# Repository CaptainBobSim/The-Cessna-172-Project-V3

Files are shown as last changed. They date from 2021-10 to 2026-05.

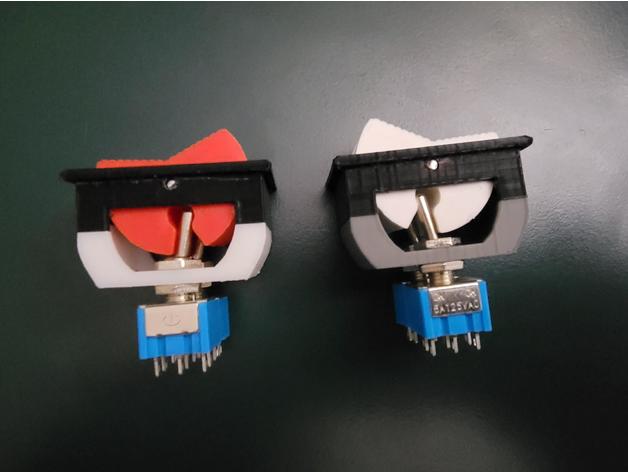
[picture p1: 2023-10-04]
Section 2A - Analog Panel/Analog Switch Panel/Steve Sweeney's Cessna_Master_Switch/images/Assembled_Side.jpg

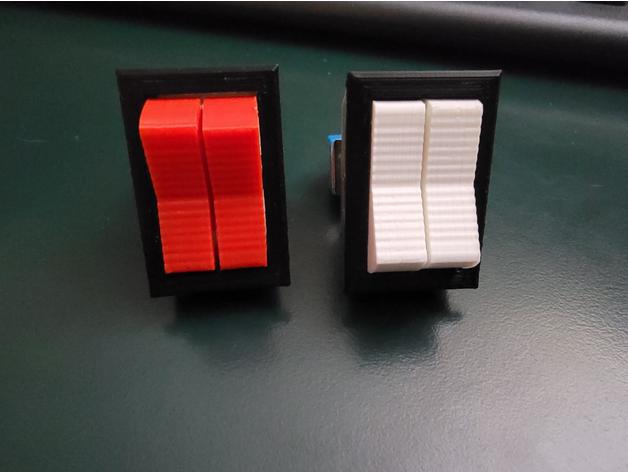
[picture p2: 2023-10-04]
Section 2A - Analog Panel/Analog Switch Panel/Steve Sweeney's Cessna_Master_Switch/images/Assembled_Front.jpg

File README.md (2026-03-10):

# The-Cessna-172-Project-V3
[Click here to download everything](https://github.com/CaptainBobSim/The-Cessna-172-Project-V3/archive/refs/heads/main.zip)
2-0-000_Full_Assembly_Section_2_2022-Dec-29_05-50-40PM-000_CustomizedView6171420002

	Your Dream Flight Simulator Has Just Landed

These plans are based on a ["Pay What You Want"](https://captainbobsim.com/product/the-cessna-172-project-files/) model. Though I could charge money for these plans, I want to give this project's plans and files away on this GitHub for free. 
### 👉[Watch the Build Videos Here](https://www.youtube.com/watch?v=Gfau2fuKCAs&list=PL3BZuuA7xo1La9Q11wTtN-bd93COms_3J)
### [💗Support development of the project on Patreon!](https://www.patreon.com/Captain_Bob) or [PayPal!](https://www.paypal.com/donate?business=H4MLB9GPEUEX4&item_name=Cessna+172+Project&currency_code=USD)
### [🛒Shop Cessna 172 Items](https://captainbobsim.com/product-category/cessna-172/)

## Table of Contents: <br />
Section 0 : Documentation <br />
Section 1 : (Archived for now) Nose (Where the PC goes) [defined as from 24" fw of firewall to the firewall]<br />
Section 2 : Structure and All Instruments/Components [defined as from the firewall to 24" aft of firewall] <br />
Section 2A/2G : INSTRUMENT PANELS and panel templates. Letter designates type. <br />
&nbsp;&nbsp;&nbsp;&nbsp;&nbsp; Section 2A : Analog Panel Template (Steam Gauges and Radio Stack) <br />
&nbsp;&nbsp;&nbsp;&nbsp;&nbsp; Section 2G : Garmin G1000 based Cessna 172 Panel <br />

Coming Later: <br />
Section 3/4 : Pilot/CoPilot Seats [defined as 24" aft of firewall to 72" aft] <br />
Section 5 : Instructor Section/Back Seat Bench <br />

### [🔨Become a Developer](https://captainbobsim.com/want-to-help/)
Email CaptainBobSim@gmail.com or go to https://captainbobsim.com/want-to-help/

### [📚C172 research/Dimensions](https://github.com/CaptainBobSim/C172-Research)

## Copyright
[Copyright _ Non Commerical_ Not for Resale](https://creativecommons.org/licenses/by-nc/4.0/)

## Spreadsheet
Top level files are usually to big to store on GitHub, so instead you can download them from the links on [this spreadsheet.](https://docs.google.com/spreadsheets/d/1PClelHtWd3HWM-4E4RQvf7FtlqrC03PmzhzorxXTbhs/edit?usp=sharing)
Please start an issue should a link not properly work.

Take a look at the [Standard components](https://docs.google.com/spreadsheets/d/1PClelHtWd3HWM-4E4RQvf7FtlqrC03PmzhzorxXTbhs/edit#gid=2116223817) the Cessna 172 Project uses.

## Issues:
We all have our issues :) If you find any that pertain to the 172 project, create a new blank issue and describe it as best you can.
Create a new issue for if a part breaks so that we can factor it into a redesign.
https://github.com/CaptainBobSim/The-Cessna-172-Project-V3/issues

## Why?
The Flight Simulation Community has given me so much and I would like to give back. Free C172 Plans were what got me into flight simulation when I was younger, and I don't want cost to be an obstacle for aspiring individuals building their own Cessna 172 Flight Sim.

If you are just getting started in Flight Simulation, I believe in you. You can do this. It will take time and hard work, but for me, it is definitely worth it, and you might find it is too.

"Everyone is smart and can be smarter."

## Special Thanks:
Thank you to Kovinator for being an absolute madlad and helping so much with the instruments! He made all of the servo small fuel instruments as well as various adaptaions of large instruments. <br />
Thank you to knector01 for making the dual potentiometer for the dimming knobs!

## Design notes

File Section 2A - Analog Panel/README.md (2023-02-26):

Hello! 
If you are looking for instruments and radios you've come to the wrong place :|

Instruments and radios are stored in Section 2 - Component Library.

In Section 2A you will find panels specific to the Analog Sim (The Main Instrument panel, switch panel, etc.)

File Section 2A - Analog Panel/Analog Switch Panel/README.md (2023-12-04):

UnfortunatelyJay VR took this switch down. Before he took it to me he licensed it to me for manufacturing, but not file sharing.

Unfortunately because of this licensing clash, the only way to get it is to source a real one or purchase the model from me: https://captainbobsim.com/product/master-avionics-switch/

Luckily Steve also made a switch, that you can find in "Steve Sweeney's" folder. As of writing I have not tested this.

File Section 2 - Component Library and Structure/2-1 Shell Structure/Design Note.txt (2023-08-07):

Happy Landings!

Note to self: Converter is https://www.zamzar.com/convert/dxf-to-pdf/

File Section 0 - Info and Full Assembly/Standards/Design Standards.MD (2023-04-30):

## GEARS
Use Module 1.5
Find the pitch diameter of the gear and divide it by 1.5 to get the amount of teeth the gear needs.
Make sure your pitch diameter is in multiples of 2 so it can be halved!

## Arduinos: 
Each pin may not draw more than 40 mA of current!
Each Arduino MEGA may not draw more than 150mA of current! [200mA is actual limit - 150mA is safety limit]
Components male, Arduino female?

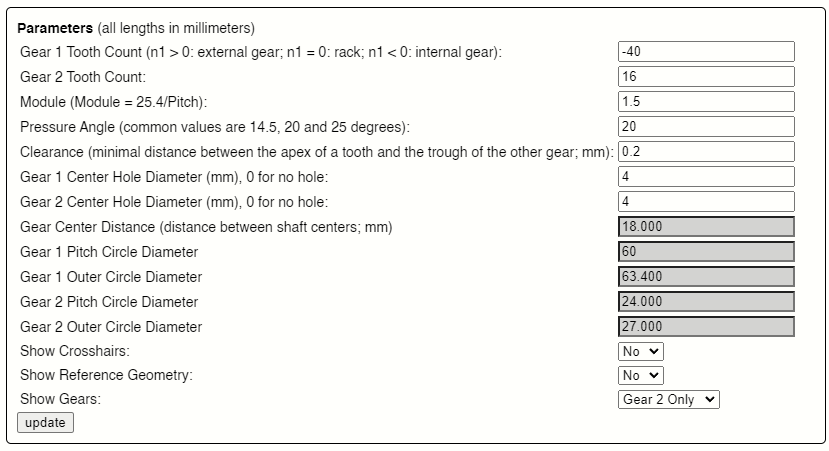
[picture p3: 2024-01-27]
Section 2 - Component Library and Structure/2-5 Instruments/SECONDARY_ADF/Source/Evolvent Design Parameters V2.png

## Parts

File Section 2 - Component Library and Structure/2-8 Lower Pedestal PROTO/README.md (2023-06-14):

Build Video Here:
Configuration Video:

🛒Buy it as a Kit or Assembled:

Welcome to the Simulator of your dreams!
Support the project here: https://captainbobsim.com/project-support/

🛩How to navigate the files? 🧭

- STLs contain all of the print files
- MobiFlight Files contain the software configuration using MobiFlight (You can merge it into your top level MobiFlight file)
- Source Files is where you'll find all of the raw files if you want to make any customizations for yourself.

__Bill 'o Materials:__
📦 3D Printed Parts
📦 Arduino Mega 2560 (can be shared with other components)
📦 
📦 

USB Extension: https://www.amazon.com/dp/B01NCA9XEI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

Pinout: 
https://www.tablesgenerator.com/markdown_tables

YOU MAY NOT SELL THESE WITHOUT PERMISSION
Unless stated otherwise in a license file within this folder, this is licenced using
**[Copyright _ Non Commerical_ Not for Resale](https://creativecommons.org/licenses/by-nc/4.0/)**
Contact CaptainBobSim@gmail.com for licensing details.

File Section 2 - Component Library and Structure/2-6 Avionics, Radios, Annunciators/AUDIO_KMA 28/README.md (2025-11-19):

[Build Video Here]() Not yet posted

[Buy it as a Kit]() Not yet available
[Buy it assembled]() Not yet available

Welcome to the Simulator of your dreams!

To navigate all of the files on your journey towards homecockpitness,
Source Files is where you'll find all of the raw files if you want to make any customizations for yourself.

Bill 'o Materials:
Arduino Mega Breakout Board System
x10 LED_PUSH_7MM
LED Blue, 5mm
LED White, 5mm
x2 LED Green, 5mm
LED Yellow, 5mm
RS16 Mini 6 Position Rotary Switch
x14 100Ω Resistor
150Ω Resistor
x2 Small ON OFF ON 3 Position Toggle SP3T
IDC 40 - Male
IDC_40 Cable
Encoder Plum 15mm
3D Printed Parts
x4 M3 Heat Set Insert (Height 4mm)
x3 M3 8mm Countersunk
x4 M3 12mm Countersunk
Shipping Label/Decal
Circuit Board

| KMA-28 | IDC 40 | Breakout Board Pin |
|---|---|---|
| 1 | GND | GND |
| 2 | 5V | 5V |
| 3 | LED_O | Digital pin 2 (PWM)  |
| 4 | LED_M | Digital pin 3 (PWM)  |
| 5 | LED_I | Digital pin 4 (PWM)  |
| 6 | VOL_A | Digital pin 5 (PWM)  |
| 7 | VOL_B | Digital pin 14 (TX3) |
| 8 | VOL_PU | Digital pin 15 (RX3) |
| 9 | HI_SW | Digital pin 16 (TX2) |
| 10 | TM_SW | Digital pin 17 (RX2) |
| 11 | ISO_SW | Digital pin 18 (TX1) |
| 12 | CREW_SW  | Digital pin 19 (RX1) |
| 13 | COM1_L | Digital pin 20 (SDA) |
| 14 | COM1_P | Digital pin 21 (SCL) |
| 15 | COM2_L | Digital pin 22 |
| 16 | COM2_P | Analog pin 0 |
| 17 | NAV1_L | Analog pin 1 |
| 18 | NAV1_P | Analog pin 2 |
| 19 | NAV2_L | Analog pin 3 |
| 20 | NAV2_P | Analog pin 4 |
| 21 | MKR_L | Digital pin 23 |
| 22 | MKR_P | Digital pin 24 |
| 23 | ICS_L | Digital pin 6 (PWM)  |
| 24 | ICS_P | Digital pin 7 (PWM)  |
| 25 | ADF_L | Digital pin 8 (PWM)  |
| 26 | ADF_P | Digital pin 9 (PWM)  |
| 27 | AUX_L | Digital pin 25 |
| 28 | AUX_P | Digital pin 26 |
| 29 | DME_L | Digital pin 27 |
| 30 | DME_P | Digital pin 28 |
| 31 | SPR_L | Digital pin 29 |
| 32 | SPR_P | Digital pin 30 |
| 33 | COM3 | Digital pin 31 |
| 34 | COM2 | Digital pin 32 |
| 35 | COM1 | Digital pin 33 |
| 36 | COM1/2 | Analog pin 5 |
| 37 | COM2/1 | Analog pin 6 |
| 38 | TEL | Analog pin 7 |
| 39 | Transmit | Analog pin 8 |
| 40 | Swap | Analog pin 9 |

YOU MAY NOT SELL THESE WITHOUT PERMISSION
**[Copyright _ Non Commerical_ Not for Resale](https://creativecommons.org/licenses/by-nc/4.0/)**
Contact CaptainBobSim@gmail.com for licensing details.

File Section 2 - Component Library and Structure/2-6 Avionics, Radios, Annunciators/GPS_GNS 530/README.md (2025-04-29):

[Build Video Here](https://youtu.be/dMBtQhVhItA)

Purchase the Circuit Board Here: http://captainbobsim.com/product/gns-530-circuit-board/

Get a Kit Here: http://captainbobsim.com/product/gns-530-kit/
Get a fully assembled unit here: http://captainbobsim.com/product/gns-530-assembled/

Welcome to the Simulator of your dreams!

To navigate all of the files on your journey towards homecockpitness,
Source Files is where you'll find all of the raw files if you want to make any customizations for yourself. I provided the circuit board outline as a dxf if anyone wants to cut their own perfboard instead of getting a PCB. I'd highly recommend a PCB however as there are approximately 130 traces.

Bill 'o Materials:

Black, White, and Clear PLA
Arduino Pro Mega 2560x11 LED White, 3mm
x8 47ƒ¶ Resistors
x14 6x6x7 LED Tactile Push Buttons
x2 IDC 40 - Male
x4 Pin Headers Row - Female
Pin Headers Row - Male
x2 ALPS_EC11EBB24C03
x2 Encoder Plum 15mm
5 Inch 640x480 LCD Display with controller
GNS 530 PCB
x8 M3 8mm Countersunk
x4 M3 Heat Set Insert (Height 4mm)
x4 20mm F to F Standoff
x6 M3 12mm Countersunk
x4 M2 8mm Countersunk
10k ƒ¶ resistor
Photoresistor (Optional)
DC Shunt
HDMI Cable 2m
12V Power Cable

Pinout for Onboard Arduino:

| Pin | Function | | |
| --- | --- | --- | --- |
| 1 | GND | GND | |
| 2 | 5V | 5V | |
| 3 | COM_SWAP | Digital pin 10 (PWM)  | Button |
| 4 | COM_POWER (BLANK!) | Digital pin 11 (PWM)  | Empty |
| 5 | COM_A | Digital pin 12 (PWM)  | Encoder |
| 6 | COM_B | Digital pin 44 (PWM)  | Encoder |
| 7 | COM_PRESS | Digital pin 45 (PWM)  | Button |
| 8 | NAV_SWAP | Digital pin 46 (PWM)  | Button |
| 9 | NAV_A | Digital pin 47 | Encoder |
| 10  | NAV_B | Digital pin 48 | Encoder |
| 11  | NAV_PRESS | Digital pin 49 | Button |
| 12  | L-FINE_A | Digital pin 50 (MISO) | Encoder |
| 13  | L-FINE_B | Digital pin 51 (MOSI) | Encoder |
| 14  | L-ROUGH_A | Digital pin 52 (SCK)  | Encoder |
| 15  | L-ROUGH_B | Digital pin 53 (SS) | Encoder |
| 16  | L_PRESS | Digital pin 33 | Button |
| 17  | CDI | Digital pin 34 | Button |
| 18  | OBS | Digital pin 35 | Button |
| 19  | MSG | Digital pin 36 | Button |
| 20  | FPL | Digital pin 37 | Button |
| 21  | VNAV | Digital pin 38 | Button |
| 22  | PROC | Digital pin 39 | Button |
| 23  | R_FINEA | Digital pin 40 | Encoder |
| 24  | R_FINEB | Digital pin 41 | Encoder |
| 25  | R_ROUGHA | Digital pin 42 | Encoder |
| 26  | R_ROUGHB | Digital pin 43 | Encoder |
| 27  | R_PRESS | Analog pin 5 | Button |
| 28  | ENT | Analog pin 6 | Button |
| 29  | CLR | Analog pin 7 | Button |
| 30  | MENU | Analog pin 10 | Button |
| 31  | DIRECT | Analog pin 11 | Button |
| 32  | RNG_DN | Analog pin 12 | Button |
| 33  | RNG_UP | Analog pin 13 | Button |
| 34  | ___(BLANK)___ | | Empty |
| 35  | ___(BLANK)___ | | Empty |
| 36  | ___(BLANK)___ | | Empty |
| 37  | ___(BLANK)___ | | Empty |
| 38  | ___(BLANK)___ | | Empty |
| 39  | PHOTORESISTOR | Analog pin 14 | Analog Input |
| 40  | ANALOG_EXTRA | Analog pin 15 | Analog Input |

Pinout for EXTRA PINS Pin Header.
| Pin | Function | Arduino Pin  |
|-----|---|---|
| 1 | GND | |
| 2 | 5V | |
| 3 | Digital pin 2 (PWM)  | Button |
| 4 | Digital pin 3 (PWM)  | Empty |
| 5 | Digital pin 4 (PWM)  | Encoder |
| 6 | Digital pin 5 (PWM)  | Encoder |
| 7 | Digital pin 14 (TX3) | Button |
| 8 | Digital pin 15 (RX3) | Button |
| 9 | Digital pin 16 (TX2) | Encoder |
|  10 | Digital pin 17 (RX2) | Encoder |
|  11 | Digital pin 18 (TX1) | Button |
|  12 | Digital pin 19 (RX1) | Encoder |
|  13 | Digital pin 20 (SDA) | Encoder |
|  14 | Digital pin 21 (SCL) | Encoder |
|  15 | Digital pin 22 | Encoder |
|  16 | Analog pin 0 | Button |
|  17 | Analog pin 1 | Button |
|  18 | Analog pin 2 | Button |
|  19 | Analog pin 3 | Button |
|  20 | Analog pin 4 | Button |
|  21 | Digital pin 23 | Button |
|  22 | Digital pin 24 | Button |
|  23 | Digital pin 6 (PWM)  | Encoder |
|  24 | Digital pin 7 (PWM)  | Encoder |
|  25 | Digital pin 8 (PWM)  | Encoder |
|  26 | Digital pin 9 (PWM)  | Encoder |
|  27 | Digital pin 25 | Button |
|  28 | Digital pin 26 | Button |
|  29 | Digital pin 27 | Button |
|  30 | Digital pin 28 | Button |
|  31 | Digital pin 29 | Button |
|  32 | Digital pin 30 | Button |
|  33 | Digital pin 31 | Button |
|  34 | Digital pin 32 | Empty |
|  35 | | Empty |
|  36 | | Empty |
|  37 | | Empty |
|  38 | | Empty |
|  39 | Analog pin 8 | Analog Input |
|  40 | Analog pin 9 | Analog Input |

YOU MAY NOT SELL THESE WITHOUT PERMISSION
**[Copyright _ Non Commerical_ Not for Resale](https://creativecommons.org/licenses/by-nc/4.0/)**
Contact CaptainBobSim@gmail.com for licensing details.

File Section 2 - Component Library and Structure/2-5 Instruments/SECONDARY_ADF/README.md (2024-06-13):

Build/Config Video Here: [Build an ADF Instrument for a Flight Sim | C172 #52 - YouTube](https://youtu.be/ojH7NXjEXp0)

🛒Buy it as a Kit or Assembled: [ADF Instrument (Kit or Assembled) - Captain Bob Flight Simulation](https://captainbobsim.com/product/adf-instrument/)

Welcome to the Simulator of your dreams!
Support the project here: https://captainbobsim.com/project-support/

🛩How to navigate the files? 🧭

- STLs contain all of the print files
- MobiFlight Files contain the software configuration using MobiFlight (You can merge it into your top level MobiFlight file)
- Source Files is where you'll find all of the raw files if you want to make any customizations for yourself.

__Bill 'o Materials:__

Black and Yellow Filament

x1 Laser Cut Acrylic Glass

x1 20mm Rotary Encoders D Shaft

x2 BYJ48 Stepper Motors & Drivers

x4 M3 8mm Screws

x8 M2 16mm Countersunk

x8 M2 Heat Set Insert (Height 3mm)

Decal Sheet

Arduino Mega 2560

Hook Up Wire

Soldering Material

x4 Panel Mounting Screws

Pinout: 
https://www.tablesgenerator.com/markdown_tables

YOU MAY NOT SELL THESE WITHOUT PERMISSION
Unless stated otherwise in a license file within this folder, this is licenced using
**[Copyright _ Non Commerical_ Not for Resale](https://creativecommons.org/licenses/by-nc/4.0/)**
Contact CaptainBobSim@gmail.com for licensing details.

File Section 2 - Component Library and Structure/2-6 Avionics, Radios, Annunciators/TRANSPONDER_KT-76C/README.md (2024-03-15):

Build Video Here: (Not yet published)
Configuration Video: (Config is too long to make a video)

📁The Gerber files for the Circuit Board can be purchased here: https://captainbobsim.com/gerbel-Transponder-KT-76C-Like

🛒The Circuit Board can be purchased here: https://captainbobsim.com/product/kt-76c-like-transponder-pcb/ 

🛒Buy it as a Kit or Assembled: (Not yet available)

Welcome to the Transponder of your dreams!
PCB files provided for Patreon supporters above First Officer Tier! Support the project here: https://captainbobsim.com/project-support/

🛩How to navigate the files? 🧭

- STLs contain all of the print files
- MobiFlight Files contain the software configuration using MobiFlight (You can merge it into your top level MobiFlight file)
- Source Files is where you'll find all of the raw files if you want to make any customizations for yourself.

__Bill 'o Materials:__
3D Printed Parts
1    Arduino Mega 2560 (can be shared with other components)
11    6x6x7 LED Tactile Push
1    IDC 30 - Male
2    IDC 30 - Female
0.25    40P Ribbon Cable (Meters)
1    RS16 Mini 5 Position Rotary Switch
1    PCB
1    Male Pin Headers (2 and 3)
1    MAX 7219 Display
1    Window Tint
6    M3 Heat Set Insert (Height 4mm)
4    M3 8mm Countersunk
2    M3 12mm Countersunk
3    47Ω Resistors

Pinout: 

| Pin | Function | Default Ard Pin |
| --- | --- | --- |
| 1 | GND | GND |
| 2 | 5V | 5V |
| 3 | IDT | D40 |
| 4 | 0 | D41 |
| 5 | 1 | D42 |
| 6 | 2 | D43 |
| 7 | 3 | D44 (PWM) |
| 8 | 4 | D45 (PWM) |
| 9 | 5 | D46 (PWM) |
| 10  | 6 | D47 |
| 11  | 7 | D48 |
| 12  | CLR | D49 |
| 13  | VFR | D50 (MISO) |
| 14  | RS_OFF | D51 (MOSI) |
| 15  | RS_SBY | D52 (SCK) |
| 16  | RS_TST | D53 (SS) |
| 17  | RS_ON | A0 |
| 18  | RS_ALT | A1 |
| 19  | DIN | A2 |
| 20  | CS | A3 |
| 21  | CLK | A4 |

YOU MAY NOT SELL THESE WITHOUT PERMISSION
Unless stated otherwise in a license file within this folder, this is licenced using
**[Copyright _ Non Commerical_ Not for Resale](https://creativecommons.org/licenses/by-nc/4.0/)**
Contact CaptainBobSim@gmail.com for licensing details.

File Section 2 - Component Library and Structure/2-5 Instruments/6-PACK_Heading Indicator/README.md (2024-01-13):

[Build Video Here](https://youtu.be/Jd7F1pjxnOc)
[Configuration Video Here](https://youtu.be/P1zUqRlHDGw)

[Buy it as a Kit or Assembled](https://captainbobsim.com/product/heading-indicator-kit-or-assembled/)
[Buy a PCB to make Wiring Easier](https://captainbobsim.com/product/heading-indicator-circuit-board/) Refer to the instructions on the product page on how to decipher the Circuit Board.

Welcome to the Heading Indicator of your dreams!

This uses a 16:40 gear ratio (you need to rotate the motor 2.5 times for every rotation of the hdg bug - ie the bug rotates .4 times as fast as the motor)

To navigate all of the files on your journey towards homecockpitness,
Source Files is where you'll find all of the raw files if you want to make any customizations for yourself.

Bill 'o Materials:
x2 BYJ48 Stepper Motors (and Drivers)
Arduino Mega 2560 (can be shared with other components)
Black, Orange, White Filament
x1 Laser Cut Acrylic Glass
x4 8mm M3 Screws
x4 15mm M3 Screws
x8 M3 Nuts
x2 Rotary Encoders D Shaft
x2 5x5x5mm Neodymium Magnets
North/South Pole Magnet
x2 Hall Effect Switches A3144/OH3144/AH3144E
Hook Up Wire
Soldering Material
8mm M3 Countersunk Screw
x4 Panel Mounting Screws 6/32" 1" Long and Nut

White Paint Marker
Orange Paint Marker

Go to video for links: https://youtu.be/Jd7F1pjxnOc

YOU MAY NOT SELL THESE WITHOUT PERMISSION
**[Copyright _ Non Commerical_ Not for Resale](https://creativecommons.org/licenses/by-nc/4.0/)**
Contact CaptainBobSim@gmail.com for licensing details.

Bill 'o Materials:
x2 BYJ48 Stepper Motors & Drivers
Arduino Mega 2560 
Black, Orange, White Filament
x1 Laser Cut Acrylic Glass
x4 8mm M3 Screws
x4 15mm M3 Screws
x8 M3 Nuts
x2 Rotary Encoders D Shaft
x2 5x5x5mm Neodymium Magnets
North/South Pole Magnet
x2 Hall Effect Switches A3144
Hook Up Wire
Soldering Material
x4 Panel Mounting Screws

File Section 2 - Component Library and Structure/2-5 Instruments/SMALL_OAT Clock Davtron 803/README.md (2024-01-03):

Build Video Here: https://youtu.be/th24fbRWOls

🛒Buy it as a Kit or Assembled: http://captainbobsim.com/shop (Not available in store as of writing)

Welcome to the Clock of your dreams! ⏰
Support the project here: https://captainbobsim.com/project-support/

🛩How to navigate the files? 🧭
- STLs contain all of the print files. 
- MobiFlight Files contain the software configuration using MobiFlight (You can merge it into your top level MobiFlight file)
- Source Files is where you'll find all of the raw files if you want to make any customizations for yourself.

__Bill 'o Materials:__
📦 3D Printed Parts
📦 Arduino Mega 2560 (can be shared with other components)
📦 1602 LCD Display
📦 (3) Tactile Momentary push switches 6mm x 6mm x 7mm
📦 (4) M3 8mm Countersunk screws
📦 (4) M2 8mm Countersunk screws
📦 (4) M2 Nuts

Pinout: 
| Item | Pin |
|---|---|
| GND | GND |
| SDA | SDA (D20 on MEGA) |
| SCL | SCL (D21 on MEGA) |
| VCC | +5V |
| OAT | D2 |
| Select  | D3 |
| Control | D4 |
YOU MAY NOT SELL THESE WITHOUT PERMISSION
Unless stated otherwise in a license file within this folder, this is licenced using
**[Copyright _ Non Commerical_ Not for Resale](https://creativecommons.org/licenses/by-nc/4.0/)**
Contact CaptainBobSim@gmail.com for licensing details.

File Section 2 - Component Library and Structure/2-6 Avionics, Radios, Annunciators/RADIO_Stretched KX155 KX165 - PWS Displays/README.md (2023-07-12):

Build/Config Video Here: [- YouTube](https://youtu.be/YGrNcZI5cK0)

Want me to print the parts for you? Contact CaptainBobSim@gmail.com

Welcome to the Radio of your dreams!
Support the project here: https://captainbobsim.com/project-support/

🛩How to navigate the files? 🧭

- STLs contain all of the print files
- MobiFlight Files contain the software configuration using MobiFlight (You can merge it into your top level MobiFlight file)
- Source Files is where you'll find all of the raw files if you want to make any customizations for yourself.

__Bill 'o Materials:__
📦 3D Printed Parts
📦 Arduino Mega 2560 (can be shared with other components)
📦 [5 and 6 digit kit DIY Radio Kits from PropWashSim](https://www.propwashsim.com/store/radio-kits)
📦 Rotary Encoder or Potentiometer (follow the wiring for your specific electronic)
📦 x8 M3 8mm screws
📦 x4 M3 10mm screws to mount to side

YOU MAY NOT SELL THESE WITHOUT PERMISSION

Unless stated otherwise in a license file within this folder, this is licenced using
**[Copyright _ Non Commerical_ Not for Resale](https://creativecommons.org/licenses/by-nc/4.0/)**
Contact CaptainBobSim@gmail.com for licensing details.

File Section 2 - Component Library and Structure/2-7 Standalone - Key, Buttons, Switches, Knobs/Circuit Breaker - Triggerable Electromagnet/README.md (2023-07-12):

[Build Video Here]()

[🛒Buy it as a Kit or Assembled](https://captainbobsim.com/product/triggerable-simulated-ga-style-circuit-breaker/)

Welcome to the Circuit Breaker of your dreams!

To navigate all of the files on your journey towards homecockpitness:

- NEW refers to an electromagnet solenoid with a smaller shaft
- OLD refers to the one first shown in my V1 video with a larger shaft
- Print "Button" if you want a GA style non pullable breaker
- Use the Pullable Circuit Breakers files if you want a pullable Airliner style breaker
- Source Files is where you'll find all of the raw files if you want to make any customizations for yourself.

__Bill 'o Materials:__
📦 3D Printed Parts
📦 Arduino Mega 2560 (can be shared with other components)
📦 Electromagnet:  https://www.amazon.com/NW-Self-holding-Electromagnet-Automation-Bidirectional/dp/B07RFF5XKF
📦 

YOU MAY NOT SELL THESE WITHOUT PERMISSION
Unless stated otherwise in a license file within this folder, this is licenced using
**[Copyright _ Non Commerical_ Not for Resale](https://creativecommons.org/licenses/by-nc/4.0/)**
Contact CaptainBobSim@gmail.com for licensing details.

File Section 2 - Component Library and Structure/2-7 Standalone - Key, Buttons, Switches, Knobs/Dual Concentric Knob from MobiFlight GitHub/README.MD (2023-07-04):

Base design from [GitHub - MobiFlight/mobiflight-templates: Simulator panel design templates and open hardware designs](https://github.com/MobiFlight/mobiflight-templates)

Uses ALPS encoder

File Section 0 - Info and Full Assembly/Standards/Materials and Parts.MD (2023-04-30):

Screws:
Screws should be Metric for smaller items and imperial for construction.
Use M4 10mm screws and M3 8mm screws wherever possible.

Wood:
Plywood should be 23/32 inch (18.26 mm) sanded plywood
Structural pieces are 2x4s, measuring 1.5 inch (38mm) by 3.5 inch (89mm).

Electronics:
All tactile push buttons are 6mm by 6mm by 7mm Usually this includes an LED in the light. to make a button taller, use a higher button.

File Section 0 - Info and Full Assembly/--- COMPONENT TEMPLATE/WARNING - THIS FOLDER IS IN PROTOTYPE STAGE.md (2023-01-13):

THIS FOLDER IS IN PROTOTYPE STAGE UNTIL THIS DOCUMENT IS DELETED.

[This is explained here](https://www.youtube.com/watch?v=dQw4w9WgXcQ)

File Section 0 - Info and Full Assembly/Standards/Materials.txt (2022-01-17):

Screws:
Screws should be Metric for smaller items and imperial for construction.
Use M4 10mm screws and M3 8mm screws wherever possible.

Wood:
Plywood should be 19/32 inch (15mm) laminated and sanded plywood
Structural pieces are 2x4s, measuring 1.5 inch (38mm) by 3.5 inch (89mm).

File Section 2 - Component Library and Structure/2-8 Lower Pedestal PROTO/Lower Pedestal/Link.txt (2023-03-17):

https://grabcad.com/library/12v-marine-and-automotive-socket-1

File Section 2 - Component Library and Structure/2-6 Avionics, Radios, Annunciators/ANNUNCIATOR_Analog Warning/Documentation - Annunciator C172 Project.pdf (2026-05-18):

Documentation - CaptainBobSim

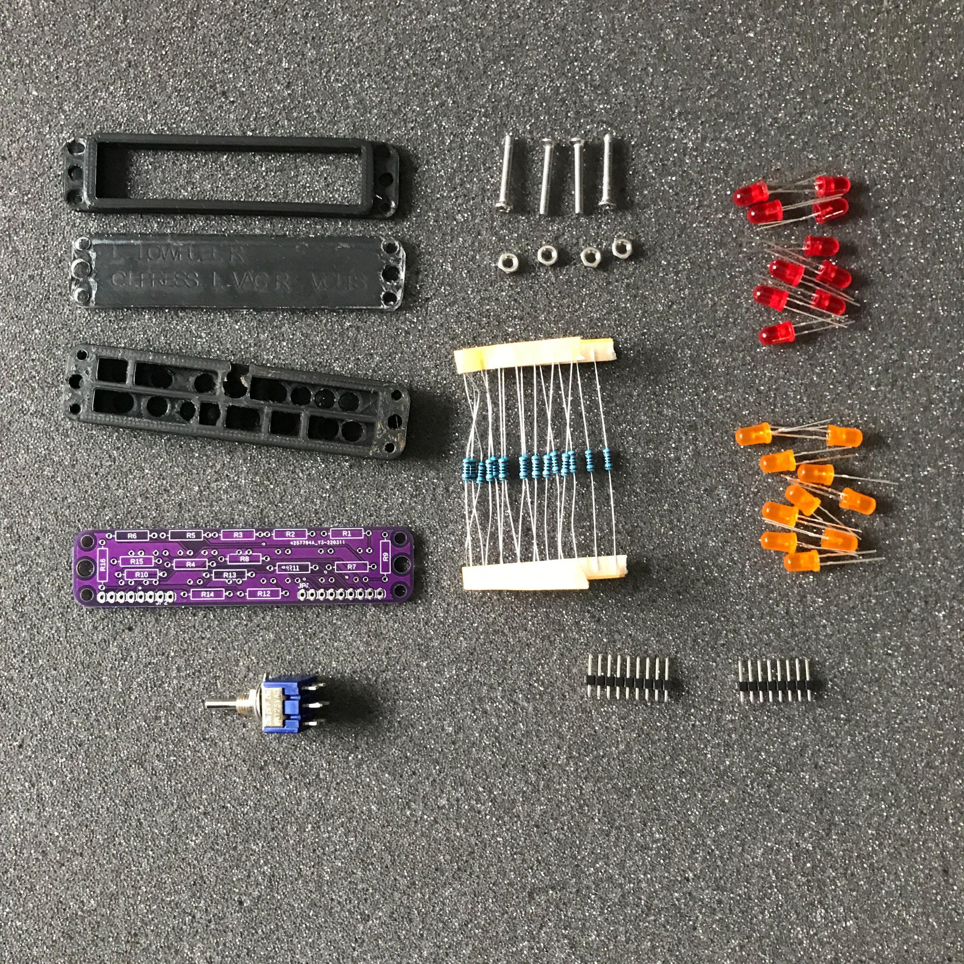
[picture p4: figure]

# Warning Annunciator Build Guide

# The Cessna 172 Project

Support the Project Here! CaptainBobSim.com/project-support

## Bill of Materials

- 3D Printed bezel
- Engraved Warning piece
- 3D Printed Light holding module
- Annunciator Circuit Board
- x20 100 ohm resistors
- x4 M3 20mm Countersunk screws
- x4 M3 nuts
- x10 Red LEDs, x10 Orange LEDs
- Pin Headers
- 3 position switch (on) off on

## Versions:

Version 5.0 Wiring is here:

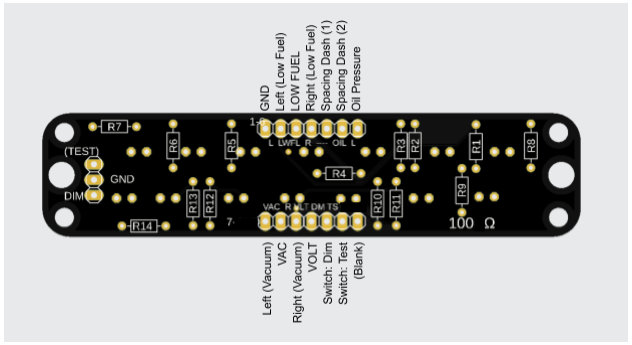
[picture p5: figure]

The circuit board may have a white dot on pin 1 and “GND” to show the relationship between the two.

## Assembly

For the assembly solder the LEDs the long end of the LEDs faces. There's a flat side of the LED, and this should align with the flat side of the circle.

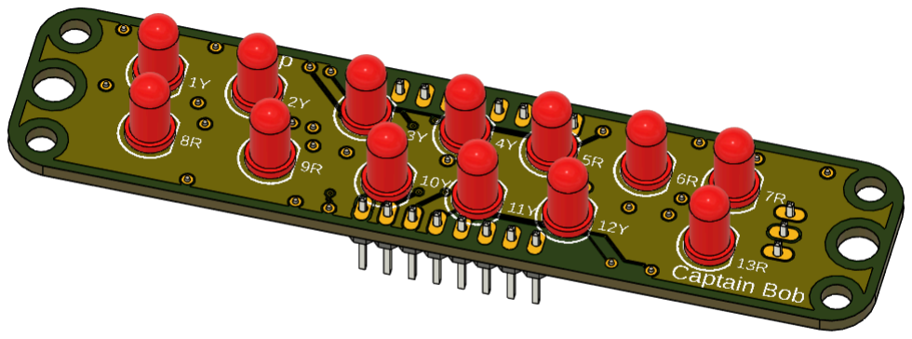
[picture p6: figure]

Note - LED Color not shown. “Y” for Yellow/Amber and “R” for red designation is shown on the front.

R is for Red
Y is for Yellow/Orange

I recommend soldering Resistors, then LEDs, then pin headers.

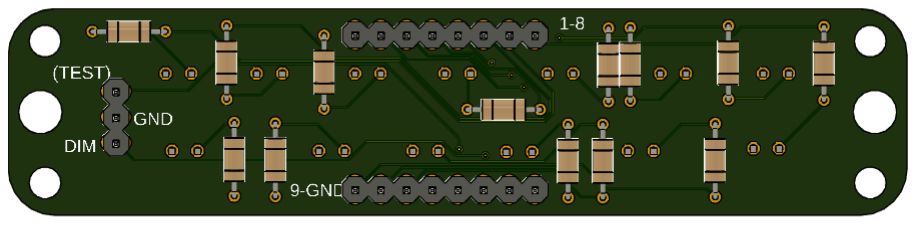
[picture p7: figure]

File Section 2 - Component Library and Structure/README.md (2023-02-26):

Looking for the Instrument Panels? Go up one folder to find the 2A or 2G panel folder.

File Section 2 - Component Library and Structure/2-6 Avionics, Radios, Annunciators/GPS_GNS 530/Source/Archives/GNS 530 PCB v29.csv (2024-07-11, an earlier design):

Qty | Value | Device | Package | Parts | Description | CATEGORY | CENTROID_NOT_SPECIFIED | DATASHEET | DESCRIPTION | DIGIKEY_DESCRIPTION | LEAD_FREE | MANUFACTURER | MAXIMUM_PACKAGE_HEIGHT | MAXIMUM_PACKAGE_HIEGHT | MF | MOUNTING_STYLE | MOUSER_PART_NUMBER | MPN | NUMBER_OF_CHANNELS | NUMBER_OF_DETENTS | OPERATING_LIFE_(CYCLES) | OPERATING_TEMP | OPERATING_TEMPERATURE | OUTPUT_TYPE | PACKAGE | PARTREV | PART_STATUS | PITCH | POPULARITY | PREFIX | RATING | RESOLUTION | ROHS | ROHS_COMPLIANCE | ROHS_COMPLIANT | SERIES | STANDARD | SUB-CATEGORY | TECHNOLOGY | TEMPERATURE_RANGE_HIGH | TEMPERATURE_RANGE_LOW | TERMINATION_STYLE | THERMALLOSS | TOLERANCE | TYPE | VOLTAGE
1 |  | PINHD-1X2 | 1X02 | EXT_BKLT | PIN HEADER |  |  |  |  |  |  |  |  |  |  |  |  |  |  |  |  |  |  |  |  |  |  |  | 98
4 |  | R-US_AXIAL-7.2MM-PITCH | RESAD724W46L381D178B | R1, R2, R3, R4 | Resistor Fixed - ANSI | Resistor |  |  |  |  |  |  |  |  |  |  |  |  |  |  |  |  |  |  |  |  |  |  |  |  |  |  |  |  |  |  |  | Fixed
2 | ALPS_EC11EBB24C03ALPS_EC11EBB24C03_0_0 | ALPS_EC11EBB24C03ALPS_EC11EBB24C03_0_0 | ALPS_EC11EBB24C03_0 | ENC1, ENC2 | Compact and highly reliable type available in many varieties |  | No | http://www.alps.com/prod/info/E/HTML/Encoder/Incremental/EC11/EC11EBB24C03.html |  | ENC | yes |  |  |  | ALPS | PCB Mount | 688-EC11EBB24C03 | EC11EBB24C03 | 2 Channel | 30 Detent | 15000 |  |  | Quadrature | ENCODER_PTH_11MM7X12MM0 |  |  |  |  | ENC | 10mA 5VDC | 15 PPR | yes |  |  |  |  |  | Rotary | +85°C | -40°C | Through Hole |  |  | Incremental
2 | EC11_ROTARY | EC11_ROTARY | SW_482016514001 | COM, NAV | Rotary Encoder Mechanical 15 Quadrature (Incremental) Vertical |  |  |  |  |  |  | Wurth Electronics | 26.9 mm |  |  |  |  |  |  |  |  |  |  |  |  | 001.000 |  |  |  |  |  |  |  |  |  |  | Manufacturer Recommendations
2 | IDC_40_PINHD-2X20 | IDC_40_PINHD-2X20 | IDC_40_2X20 | IDC_40A, OUTBOUND | PIN HEADER
14 | LED_PUSH_7MM | LED_PUSH_7MM | LED_PUSH_7MM | -D->, CDI, CLR, COM_SWAP, DN, ENT, FPL, MENU, MSG, NAV_SWAP, OBS, PROC, UP, VNAV
1 | MEGA_PRO_EMBED_CH340G_/_ATMEGA2560 | MEGA_PRO_EMBED_CH340G_/_ATMEGA2560 | MODULE_MEGA_PRO_EMBED_CH340G_/_ATMEGA2560 | ARDUINO_PRO_MEGA | Mega 2560 PRO (Embed) CH340G/ATmega2560-16AU |  |  |  |  |  |  | Robotdyn |  |  |  |  |  |  |  |  |  |  |  |  |  | 12/May/2017 |  |  |  |  |  |  |  |  |  |  | Manufacturer Recommendations
1 | PINHD-1X3 | PINHD-1X3 | 1X03 | BACKLIGHT | PIN HEADER | Headers |  |  | Header, Straight, 3 Position |  |  | Generic |  |  |  |  |  | Generic |  |  |  |  | Generic |  |  |  | Active | 0.100 (2.54mm)" |  |  |  |  |  | Generic |  | Generic |  | Headers, Male Pins |  |  |  |  |  |  | Board to Board or Cable, Unshrouded, Through Hole, Straight

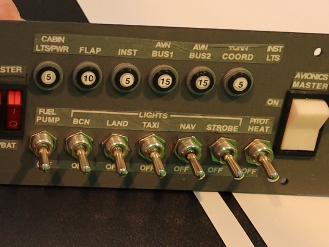
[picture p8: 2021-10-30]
Section 2 - Component Library and Structure/2-7 Standalone - Key, Buttons, Switches, Knobs/Circuit Breakers - Dummy/CBs.PNG

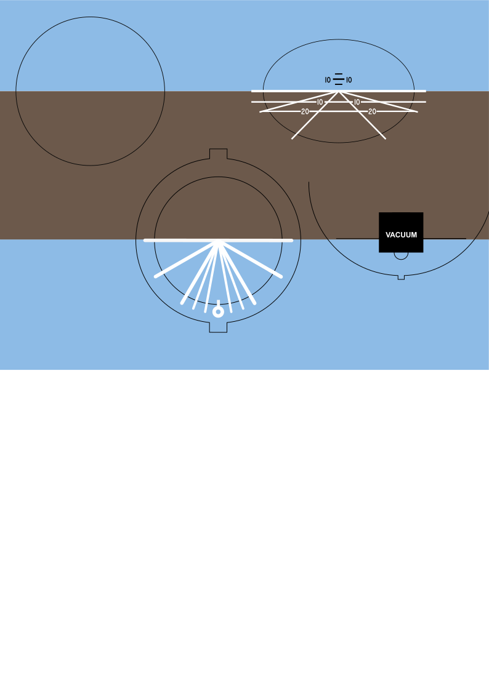
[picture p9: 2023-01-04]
Section 2 - Component Library and Structure/2-5 Instruments/6-PACK_Attitude Indicator/Source/Decals/Updated Attitude Indicator Deals.png

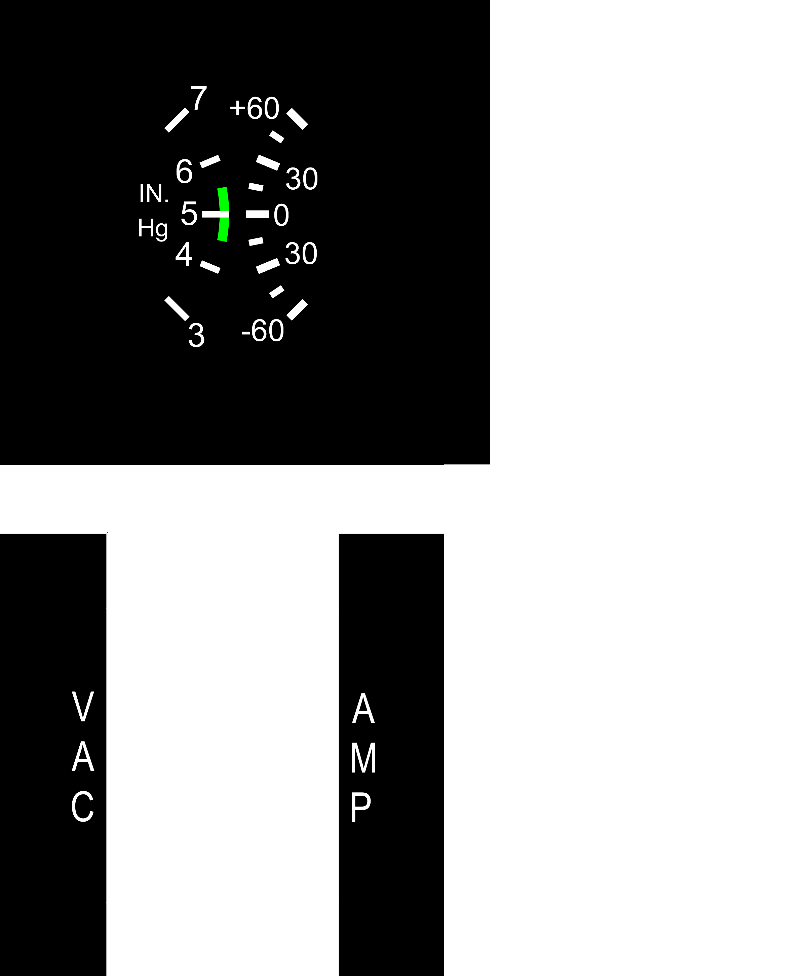
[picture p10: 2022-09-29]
Section 2 - Component Library and Structure/2-5 Instruments/Ξ SMALL_Engine Instruments PROTO/Source/Decals/Vac Amp Indicator.png

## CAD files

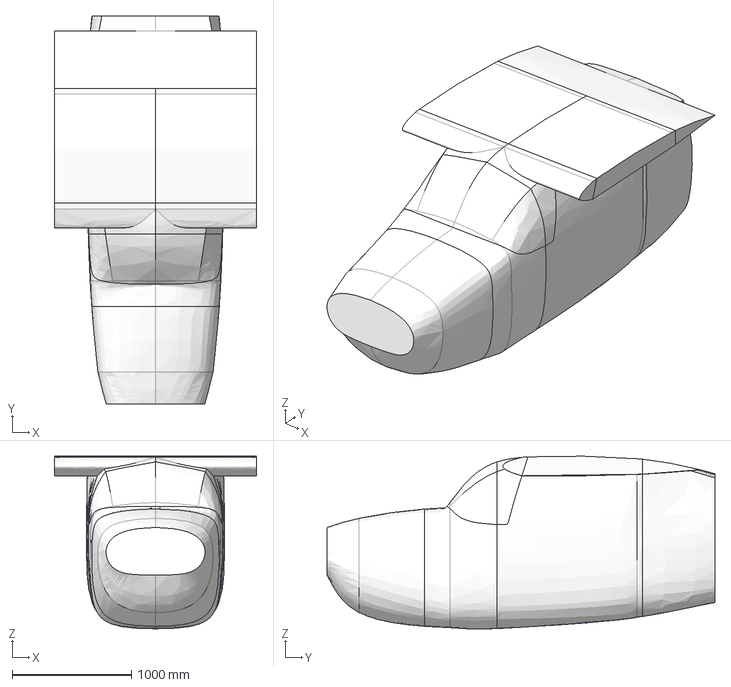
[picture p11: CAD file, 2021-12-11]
Section 0 - Info and Full Assembly/0-1 Full Shell Structure/0-1-000 V5 Form Shell Assembly_v50.step
1695.3 x 3255.0 x 1449.3 mm

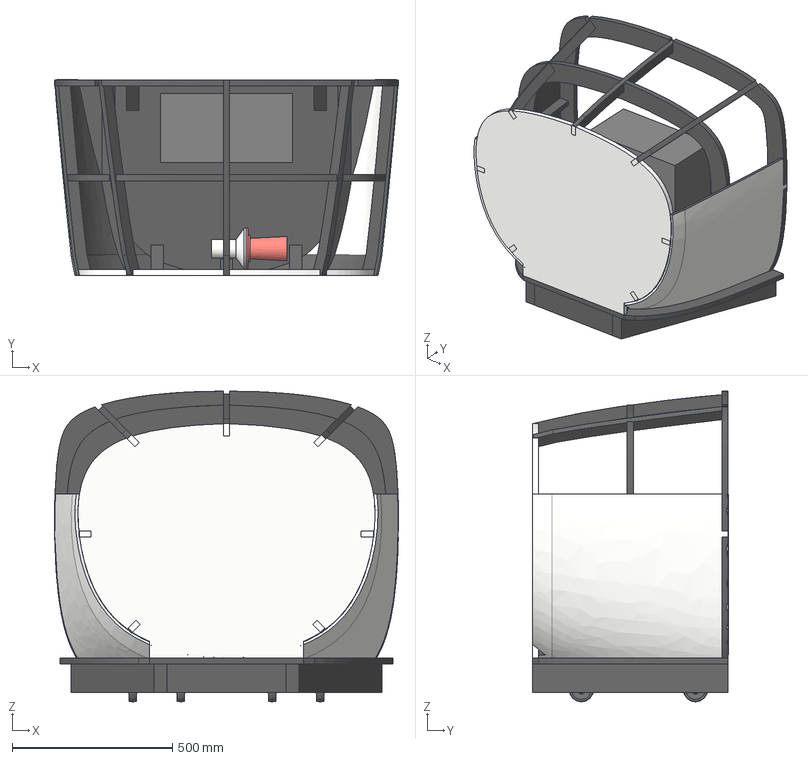
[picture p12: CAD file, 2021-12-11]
Section 1 - Nose/1-0 Full Section 1 Assy v20/1-0 Full Section 1 Assy_v24.step
1071.7 x 611.2 x 968.4 mm
PC
Ribs
Stringers
Sheathing
Support Blocks
1-1-202 Wheel Spacers
1-1 Wood
Harbor Freight Awooga Horn

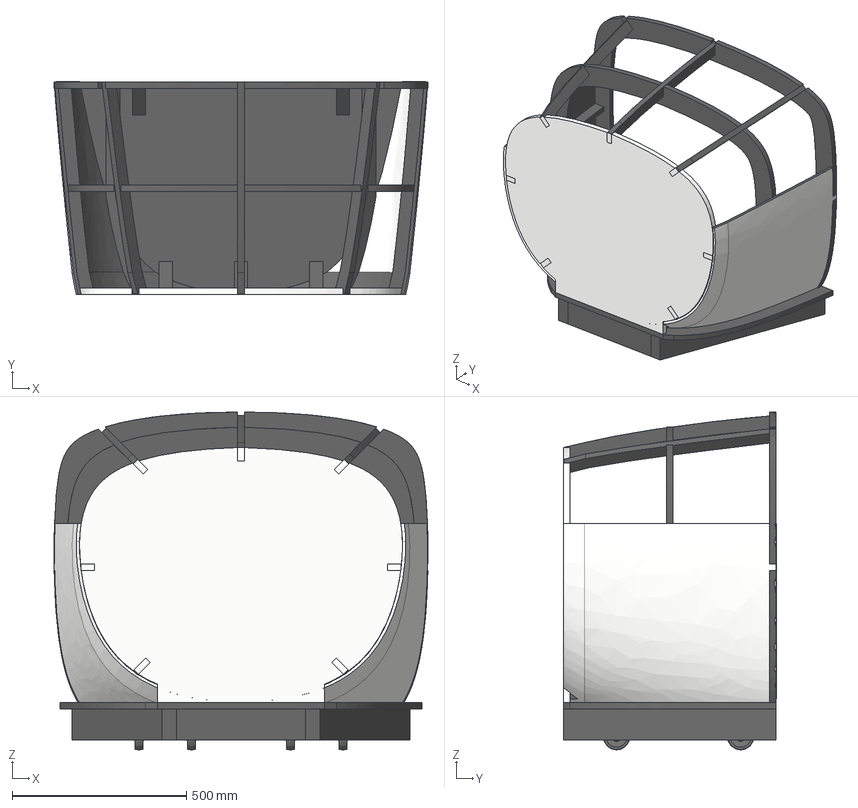
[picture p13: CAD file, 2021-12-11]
Section 1 - Nose/1-1 Shell Complete Assy v85/1-1 Shell Complete Assy_v88.step
1071.7 x 611.2 x 968.4 mm
Ribs
Stringers
Sheathing
Support Blocks
1-1-202 Wheel Spacers
1-1 Wood

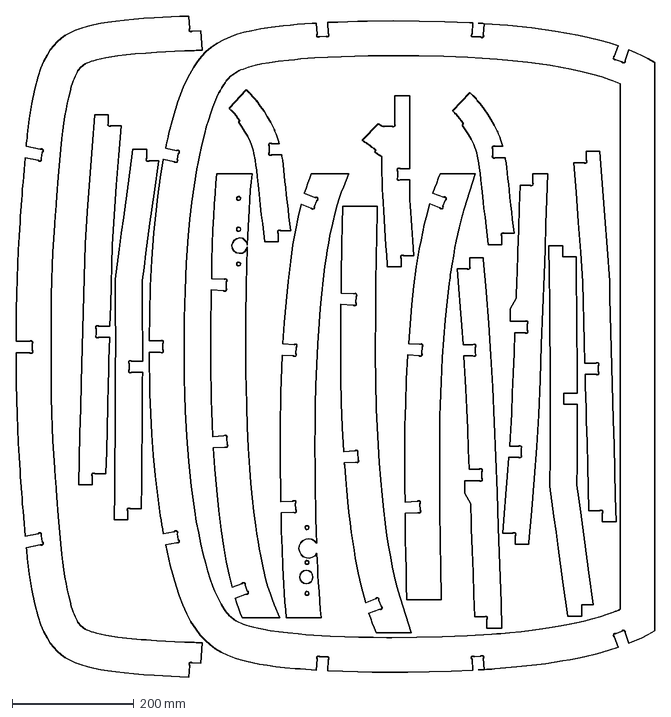
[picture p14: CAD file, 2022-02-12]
Section 2 - Component Library and Structure/2-1-000 Shell Structure/v194 DXF Full Shell.dxf
1050.9 x 1087.7 mm

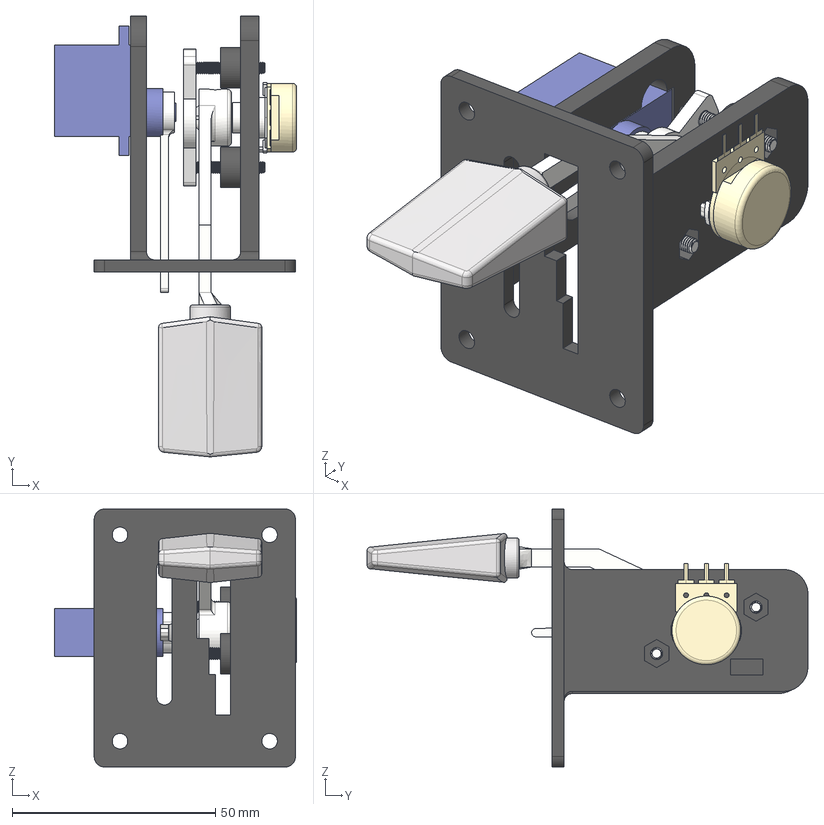
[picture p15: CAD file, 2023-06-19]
Section 2 - Component Library and Structure/2-4 Secondary Controls - Flap, Trim, Throttle, Mixture/Flaps/Source/Flap Assy v81.step
59.6 x 108.5 x 63.5 mm
Faceplate
Servo Lever
Servo Motor
potentiometerb10k
92010A128_Passivated 18-8 Stainless Steel Phillips Flat Head Screw x 2
Potentiometer Lever
Flap Handle
Tension Lock

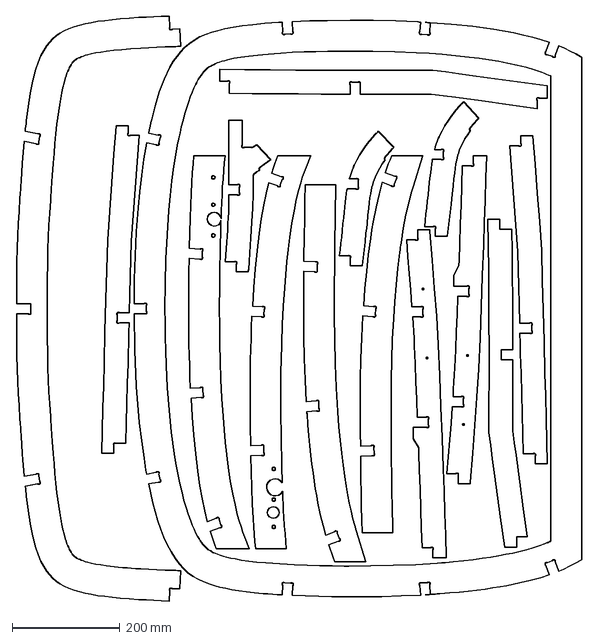
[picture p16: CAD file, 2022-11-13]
Section 2 - Component Library and Structure/2-1 Shell Structure/v214 DXF Full Shell.dxf
1050.9 x 1087.7 mm

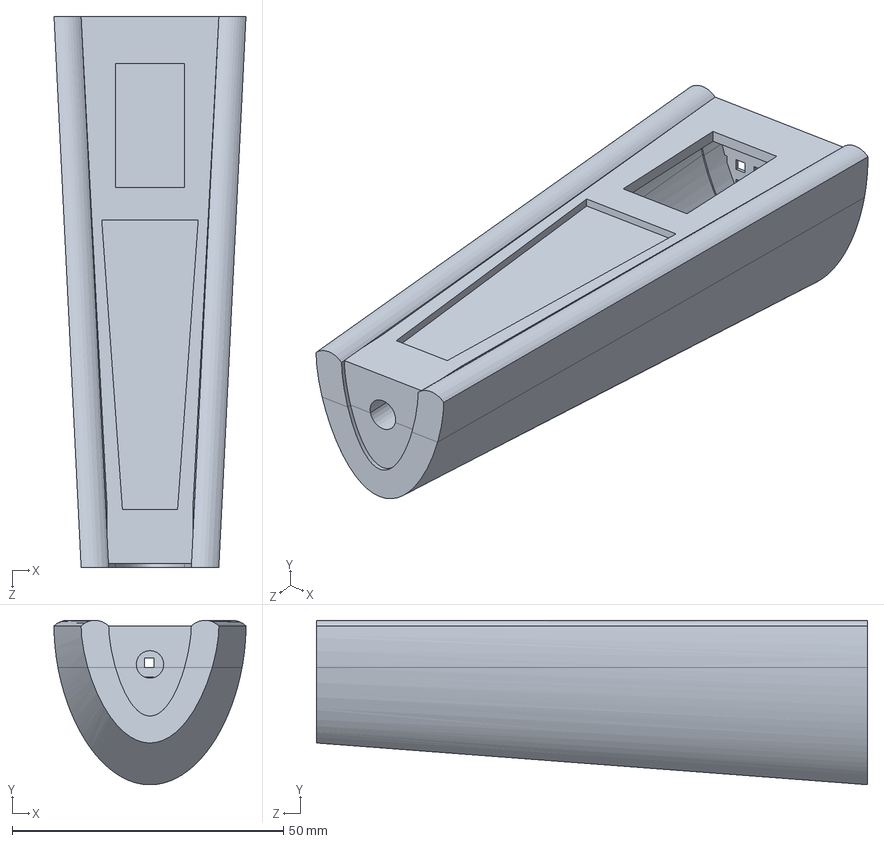
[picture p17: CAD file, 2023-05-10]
Section 2 - Component Library and Structure/2-7 Standalone - Key, Buttons, Switches, Knobs/Cessna Microphone (Thanks Everett!)/CessnaMicrophone.SLDASM
35.4 x 30.3 x 101.6 mm

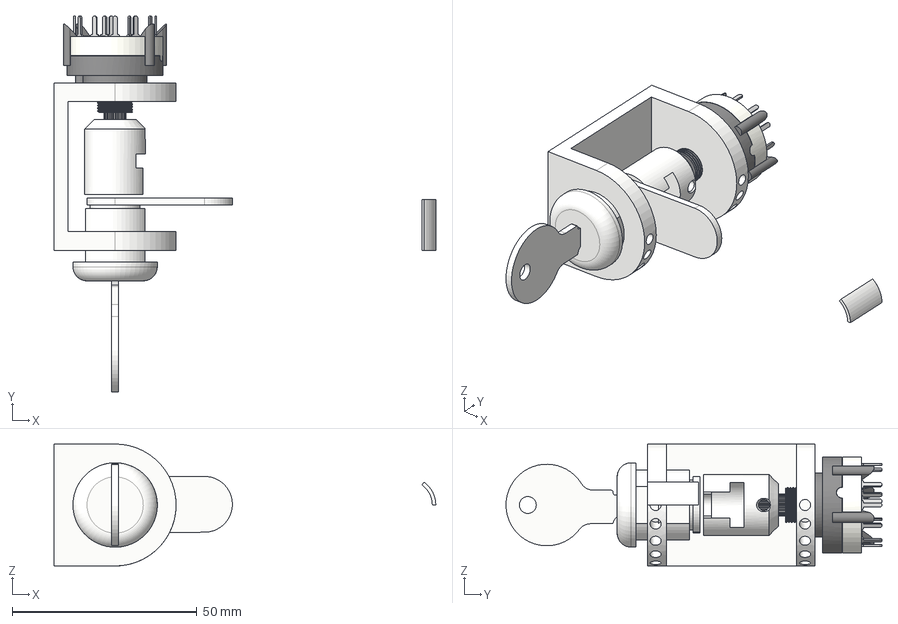
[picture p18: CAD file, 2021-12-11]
Section 2 - Component Library and Structure/2-7 Standalone - Key, Buttons, Switches, Knobs/Start Key/Key Assy_v25.step
103.3 x 101.8 x 33.0 mm
Structure
Shaft
Arm
Key
ROTARY_BODEM
ROTARY_PIN_OUTER x 12
ROTARY_INNER_PIN x 3
ROTARY_TOP
ROTARY_ROTOR
ROTARY_ROTOR_PIN x 3
SPRING
BALL_3MM x 2
ROTARY_NUT
ROTARY_LOCK_RING
Connector
Key Washer_Spacer
Flush Key Position

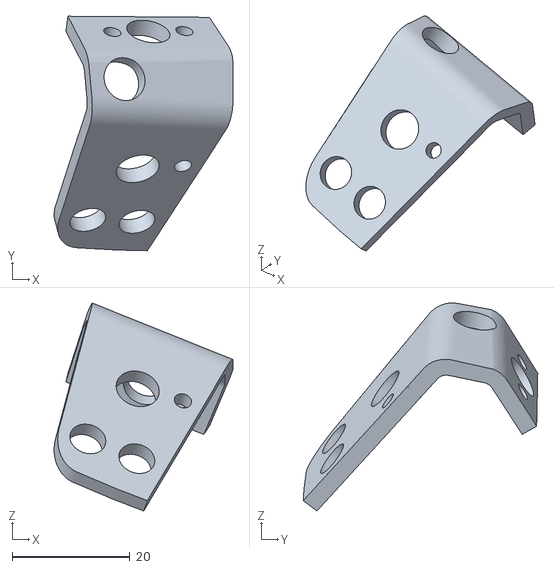
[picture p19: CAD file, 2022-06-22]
Section 2 - Component Library and Structure/2-3 Primary Controls - Yoke, Rudder/Ξ PROTO Static Yoke Assembly (Results may vary)/172R Yoke STLs/Upper left assembly.stl
30.4 x 39.9 x 35.4

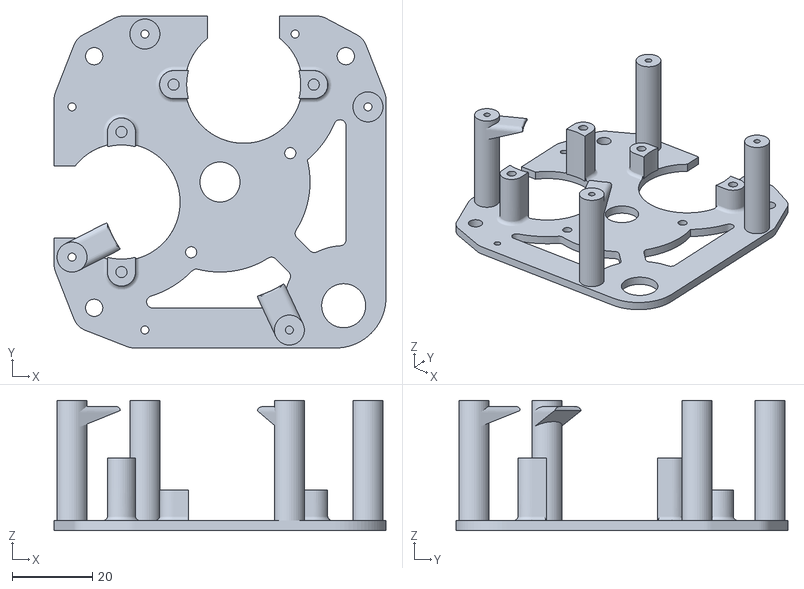
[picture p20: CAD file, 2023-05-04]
Section 2 - Component Library and Structure/2-5 Instruments/6-PACK_Altimeter/STLs/Mirror Mirror Right Knob/Mirror Motor Mount Assembly.stl
82.9 x 82.9 x 32.5

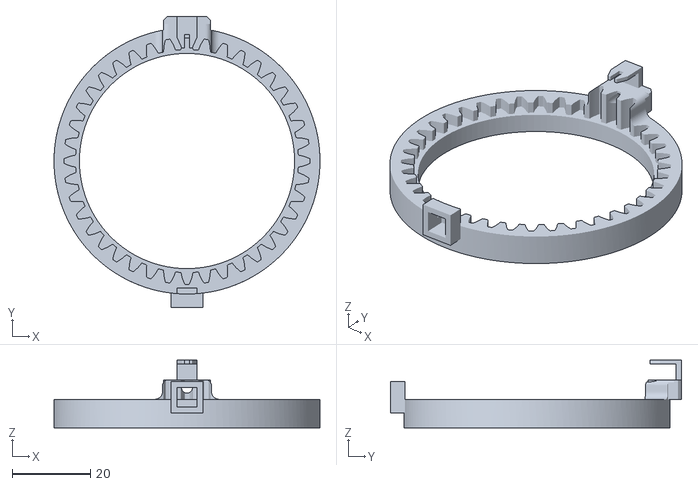
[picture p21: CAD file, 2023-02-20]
Section 2 - Component Library and Structure/2-5 Instruments/6-PACK_Heading Indicator/STLs/Ring Gear Assy.stl
68.0 x 74.5 x 17.3

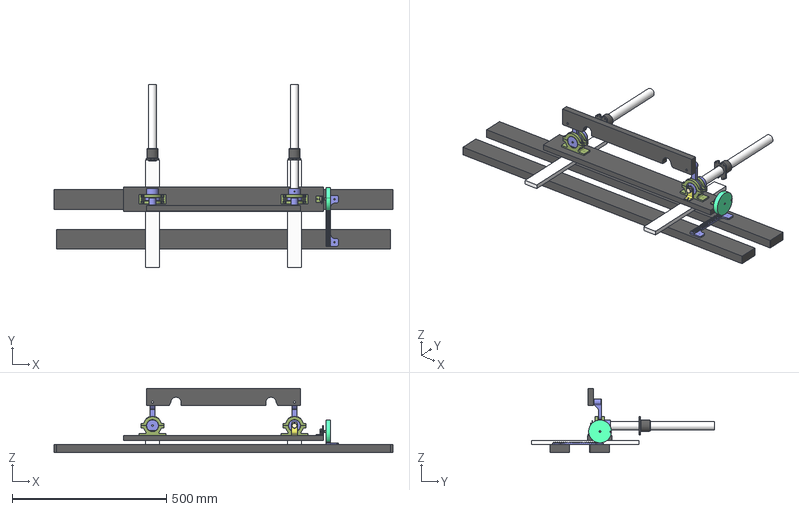
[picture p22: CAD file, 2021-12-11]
Section 2 - Component Library and Structure/2-3 Primary Controls - Yoke, Rudder/Ξ PROTO Static Yoke Assembly (Results may vary)/Yoke Assembly_v83.step
1098.4 x 593.8 x 208.7 mm
2-3-001 Cessna Yoke Grommet v2
Sketch :)
Pitch Pinion Sensor
Simulated Simple Gear
Support Pillow Ring, Arm
Pillow Blocks
Arm
Bottom Support Arm
Support Pillow Ring, Arm(Mirror)
Pillow Blocks(Mirror)
Roll Axis Mount
Drawer Roller Assy
Yoke Poles Left
Yoke Poles(Mirror)
potentiometerb10k x 2
c152+yoke+back x 2
c152+yoke+front+with+logo x 2

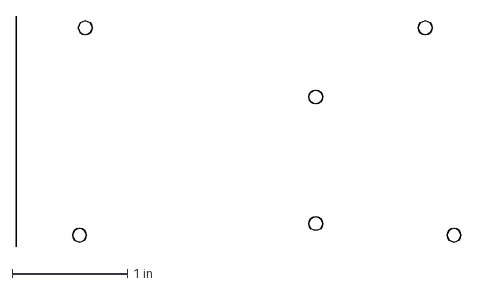
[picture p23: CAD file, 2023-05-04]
Section 0 - Info and Full Assembly/Arduino Mega Holes.dxf
3.86 x 2.00 in

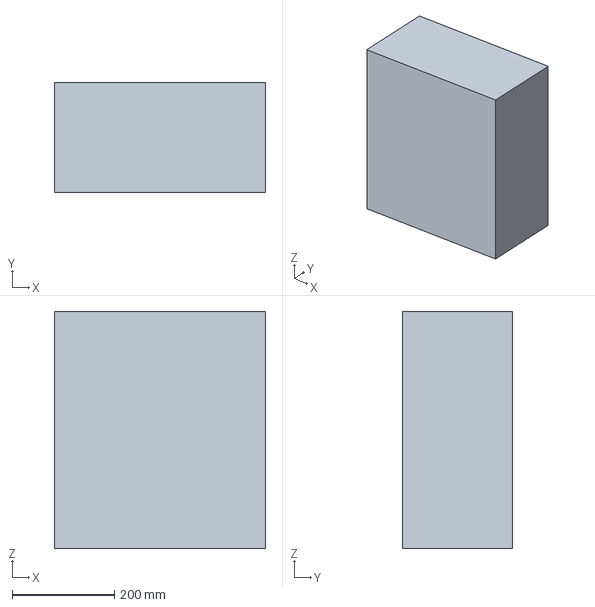
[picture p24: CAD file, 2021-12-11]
Section 1 - Nose/1-5 PC/1-5-000 PC_v2.step
412.8 x 215.9 x 463.5 mm

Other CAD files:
Section 2 - Component Library and Structure/2-5 Instruments/6-PACK_Altimeter/STLs/Motor Mount Assembly.stl
Section 1 - Nose/1-6 Aux Easter Egg Systems/Harbor Freight Awooga Horn_v2.step
Section 2 - Component Library and Structure/2-1 Shell Structure/2-1-500 Windshield.step
Section 2 - Component Library and Structure/2-3 Primary Controls - Yoke, Rudder/Ξ PROTO Static Yoke Assembly (Results may vary)/172R Yoke STLs/Left Back.stl
Section 0 - Info and Full Assembly/0-1 Full Shell Structure/0-1-001 CANVAS for Reference_v5.step
Section 1 - Nose/1-0 Full Section 1 Assy v20/1-0 Full Section 1 Assy_v24.f3d
Section 1 - Nose/1-5 PC/1-5-000 PC_v2.f3d
Section 1 - Nose/1-6 Aux Easter Egg Systems/Harbor Freight Awooga Horn_v2.f3d
Section 2 - Component Library and Structure/2-1 Shell Structure/v214 DXF Full Shell.dwg
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

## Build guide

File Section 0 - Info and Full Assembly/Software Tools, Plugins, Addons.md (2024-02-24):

## Microsoft Flight Simulator

https://flightsim.to/file/35759/msfs-pop-out-panel-manager
https://flightsim.to/file/36500/ready-to-fly-button-skipper
Not really but maybe cool https://flightsim.to/file/19345/msfs-2020-google-map-replacement
https://flightsim.to/file/34176/msfs-world-map-landmarks-permanently-off
https://github.com/pimarc/pms50-gns530

## Addon Aircraft

C172 Livery: Civil Air Patrol https://liveries.to/usafnukem/civil-air-patrol-c172-g1000

## GitHub

Download only a folder (not entire repo) https://download-directory.github.io/
Markdown Table Generator: https://www.tablesgenerator.com/markdown_tables

## Online Tools/Generators

Image measure given a dimension: https://eleif.net/photo_measure.html
Spur Gear Generator: *Recently I've Been Using This One* https://evolventdesign.com/pages/calculators
I prefer this instead of Fusion, because Fusion doesn't let you preview it.
Neither really lets you change it later, so I prefer this one, where I can just delete and paste the new sketch.

Not used anymore: https://www.engineersedge.com/calculators/spur_gear_calculator_and_generator_15506.htm

Rack/Pinion Generator: http://www.jeromeleary.com/gears/
Finger Box maker: https://en.makercase.com/#/basicbox

GT2 Pulley Collection: [Printables](https://www.printables.com/model/333720-gt2-pulley-the-big-collection-updated)

## File Converters

DWG to SVG: https://www.autodwg.com/dwg2svg/

Rotate an .STL for so you can just drag it: https://www.prusa3d.com/page/prusaslicer_424/ (export as STL)

## Fusion 360 Plugins:

Manufacturing Dogbone Generator: https://github.com/DVE2000/Dogbone
Settings: Tool Diameter .125", offset .1" Static, Normal, From Top Face 
Exporting a face as a dxf without making a sketch: https://github.com/tapnair/Export2D
Export just a few F360: https://github.com/tapnair/Project-Archiver
Export every fusion 360 file (for backup or GitHub): https://github.com/Jnesselr/fusion-360-total-exporter
SnapEDA: https://apps.autodesk.com/FUSION/en/Detail/Index?id=5446990520022318629&appLang=en&os=Win64&autostart=true

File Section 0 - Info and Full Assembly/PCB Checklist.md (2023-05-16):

- [ ] Ground Plane on bottom
- [ ] Stay Spicy airplane :)
- [ ] Autoroute Traces
- [ ] Write Version Number on PCB
- [ ] CaptainBobSim.com
- [ ] Write all component names
- [ ] Pinouts for everything

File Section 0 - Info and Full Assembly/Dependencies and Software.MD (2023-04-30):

## Dependencies
OPEN SOURCE :) MobiFlight Configuration Software
Proprietary :| FlightSimMaker G1000 Buy files here: https://www.flightsimmaker.com/category/all-products
Proprietary :| Master/Avionics Switch: https://www.thingiverse.com/thing:2794629 - You'll have to buy this from me as of now because of licensing: https://captainbobsim.com/product/master-avionics-switch/  
Saitek Pro Yoke GrabCAD Model: https://grabcad.com/library/saitek-pro-flight-cessna-yoke-system-1

## Software used:
OPEN SOURCE :) Inkscape 
Proprietary :| MSFS2020
Proprietary and Expensive :( Fusion 360 CAD software

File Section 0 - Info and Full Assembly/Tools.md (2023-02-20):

Tools Used Frequently (Online)
https://eleif.net/photo_measure.html

Spur Gear Generator:

*Recently I've Been Using This One*
https://evolventdesign.com/pages/calculators

I prefer this instead of Fusion, because Fusion doesn't let you preview it.
Neither really lets you change it later, so I prefer this one, where I can just delete and paste the new sketch.
https://www.engineersedge.com/calculators/spur_gear_calculator_and_generator_15506.htm

Yoke Rack/Pinion Generator
http://www.jeromeleary.com/gears/

## File Converters
DWG to SVG: https://www.autodwg.com/dwg2svg/

Rotate an .STL for so you can just drag it in: https://meshmixer.com/download.html

## Fusion 360 Plugins:
Manufacturing Dogbone Generator: https://github.com/DVE2000/Dogbone
Settings: Tool Diameter .125", offset .1" Static, Normal, From Top Face 

Exporting a face as a dxf without making a sketch: https://github.com/tapnair/Export2D

Export every fusion 360 file (for backup or GitHub): https://github.com/Jnesselr/fusion-360-total-exporter

Box maker: https://en.makercase.com/#/basicbox

SnapEDA: https://apps.autodesk.com/FUSION/en/Detail/Index?id=5446990520022318629&appLang=en&os=Win64&autostart=true

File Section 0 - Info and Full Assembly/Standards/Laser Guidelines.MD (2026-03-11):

Universal laser cutters use eight RGB colors: 00000 (black), ff0000 (red), 00ff00 (green), ffff00 (yellow), 0000ff (blue), ff00ff (magenta), 00ffff (cyan), ff6600 (orange).
The colors I assign these to is here:

|HEX|Color|RGB Value|Description|
|-|-|-|-|
|00000|(black)|RGB: 0	 	0 	0|FOR FILL / ENGRAVE / ETCHING TEXT|
|ff0000|(red)|RGB: 255 	0 	0|FOR LINES (Done last)|
|00ff00|(green)|RGB: 0	 	255 	0|FOR 2ND TEXT/AUX Stronger Etch|
|0000ff|(blue)|RGB: 0	 	0 	255|FOR "Scoring" going through as a strong etch.3RD TEXT/AUX Even Stronger Etch|
|ffff00|(yellow)|RGB:255	 	255 	0|FOR CUTTING PAPER (ie Labels) USE THIS ONE not orange :)|
|ff6600|(orange)|RGB: 255 	102 	0|FOR CUTTING PAPER OUTLINE/PAPER AUX 2 (Cut Label Entirely)|
|ff00ff|(magenta)|RGB: 255 	0 	255|FOR ALLIGNMENT - Do not set this to actually fire anything! You can set this to the size of your material and jog the head to it.|
|00ffff|(cyan)|RGB: 0	 	255 	255|FOR ETCHING PAPER (ie to test on paper first)|

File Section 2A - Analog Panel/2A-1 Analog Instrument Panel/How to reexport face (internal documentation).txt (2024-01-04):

## This is a developer doc, you don't have to pay attention :D

- PANEL Trace: File used for cutting
- PANEL ENGRAVE

SOURCE: 
- RAW: Directly from F360, will not have mirrored splines

To update the DXF:
- Select all faces from Fusion 360 and project them to a sketch
- Export DXF into NEW file
- Import 
- Rename PANEL TRACE

Export as Poster Mode PDF page by page

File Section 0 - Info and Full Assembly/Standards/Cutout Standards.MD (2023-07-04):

Push Pull Switches should have cutout of 38mm by 24mm with the hole of 8mm centered on the rectangle.

Small toggles should have cutout of ___ _ with diameter of _ _

Large toggles should have cutout of _ _ with diameter of _ _

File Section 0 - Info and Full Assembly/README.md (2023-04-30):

## Hello there!
This folder contains no plans, just information and top level stuff.
You'll likely spend most of your time in Section 2

Go to https://a360.co/3fVHbfW for the top level assembly model.
Top Level Files in this GitHub may not represent the most up to date version of the project.

Section Breakdown/Definitions
Section 0 : Documentation
Section 1 : (Shelved for now) Nose (Where the PC goes) [defined as from 24" fw of firewall to the firewall]
Section 2 : Structure and All Instruments/Components [defined as from the firewall to 24" aft of firewall]
Section 2A/2G : INSTRUMENT PANELS and panel templates. Letter designates type.
      Section 2A : Analog Panel Template (Steam Gauges and Radio Stack)
      Section 2G : Garmin G1000 based Cessna 172 Panel

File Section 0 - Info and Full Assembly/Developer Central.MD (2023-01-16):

Not a developer yet? [Become a Developer Here](https://captainbobsim.com/want-to-help/) or email CaptainBobSim@gmail.com

Well Hello Fellow Developers!
Thank you so much for all you do!

### Licensing
Your work is very valuable to the flight simulation community! I want to make sure that I respect your hard work.

As a contributor/developer you have the ability to set folder level licenses, described in the (["What are these.MD"](https://github.com/CaptainBobSim/The-Cessna-172-Project-V3/blob/main/Section%200%20-%20Info%20and%20Full%20Assembly/FOLDER%20LEVEL%20LICENSES%20-%20for%20contributer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) file under ["Section 0 - Info and Full Assembly/FOLDER LEVEL LICENSES - for contributers/"](https://github.com/CaptainBobSim/The-Cessna-172-Project-V3/tree/main/Section%200%20-%20Info%20and%20Full%20Assembly/FOLDER%20LEVEL%20LICENSES%20-%20for%20contributer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)
This lets you to choose to use the default license, make their work Open-Source, or make their files so that nobody (including me) can sell their work.

### What to work on?
Everything is managed via [Issues](https://github.com/CaptainBobSim/The-Cessna-172-Project-V3/issues) and the [Project](https://github.com/users/CaptainBobSim/projects/2/views/1)
You can choose anything in the "No Status" column of the Project. 

If there's something you want to work on, make an [issue for the part](https://github.com/CaptainBobSim/The-Cessna-172-Project-V3/issues/new), and assign it to yourself.

### Get GitHub to Sync
To sync the repository with your computer, use [GitHub Desktop](https://desktop.github.com/)
(https://postimg.cc/K46SXBBN)
Press the <> Code button, and select "Open with GitHub Desktop"

### Contact
If you ever have any questions at all feel free to @ mention me in a discussion/issue on GitHub, Discord, Instagram or email me CaptainBobSim@gmail.com.

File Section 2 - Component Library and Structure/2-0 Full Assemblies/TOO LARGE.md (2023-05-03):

https://a360.co/3q0kIlc

The file is too large! Instead use this link and download it directly!
⠀⠀⠀⠀⠀⠀⠀⠀⠀⠀⠀⠀⠀⢀⣀⣀⡀⠀⠀⠀⠀⠀⠀⠀⠀⠀⠀⠀⠀⠀
⠀⠀⠀⠀⠀⠀⠀⠀⠀⠀⠀⠀⣰⣿⣿⣿⣿⣆⠀⠀⠀⠀⠀⠀⠀⠀⠀⠀⠀⠀
⠀⠀⠀⠀⠀⠀⠀⠀⠀⠀⠀⠀⣿⣿⣿⣿⣿⣿⠀⠀⠀⠀⠀⠀⠀⠀⠀⠀⠀⠀
⠀⠀⠀⠀⠀⠀⠀⠀⠀⣀⣠⡄⠹⣿⣿⣿⣿⠏⣠⣄⣀⠀⠀⠀⠀⠀⠀⠀⠀⠀
⠀⠀⠀⠀⠀⠀⣠⣴⣾⣿⣿⣿⣦⣈⡙⢉⣁⣴⣿⣿⣿⣷⣦⣄⠀⠀⠀⠀⠀⠀
⠀⠀⠀⠀⣠⣾⣿⣿⣿⣿⣿⣿⣿⣿⣿⣿⣿⣿⣿⣿⣿⣿⣿⣿⣷⣄⠀⠀⠀⠀
⠀⠀⠀⣰⣿⣿⣿⣿⣿⣿⣿⣿⣿⣿⣿⣿⣿⣿⣿⣿⣿⣿⣿⣿⣿⣿⣆⠀⠀⠀
⠀⠀⢠⣿⢿⣿⣿⣿⣿⣿⣿⣿⣿⣿⣿⣿⣿⣿⣿⣿⣿⣿⣿⣿⣿⡿⣿⡄⠀⠀
⠀⠀⢼https://a360.co/3q0kIlc⡧⠀⠀
⠀⠀⠀⠀⠀⣿⣿⣿⣿⣿⣿⣿⣿⣿⣿⣿⣿⣿⣿⣿⣿⣿⣿⣿⣿⠁⠀⠀⠀⠀
⠀⠀⠀⠀⠀⠸⣿⣿⣿⣿⣿⣿⣿⣿⣿⣿⣿⣿⣿⣿⣿⣿⣿⣿⠏⠀⠀⠀⠀⠀
⠀⠀⠀⠀⠀⠀⠈⠻⣿⣿⣿⣿⣿⣿⣿⣿⣿⣿⣿⣿⣿⣿⡿⠋⠀⠀⠀⠀⠀⠀
⠀⠀⠀⠀⠀⠀⠀⠀⠀⠉⠛⠛⠿⠿⠿⠿⠿⠿⠟⠛⠋⠁⠀⠀⠀⠀⠀⠀⠀⠀
⠀⠀⠀⠀⠀⠀⠀⠀⠀⠀⣿⣿⣶⠀⠀⠀⠀⢰⣾⣿⡇⠀⠀⠀⠀⠀⠀⠀⠀⠀
⠀⠀⠀⠀⠀⠀⠀⠀⠀⠀⠉⠉⠉⠀⠀⠀⠀⠈⠉⠉⠁⠀⠀⠀⠀⠀⠀⠀⠀⠀

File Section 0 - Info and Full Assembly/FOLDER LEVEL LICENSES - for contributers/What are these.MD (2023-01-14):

Why?
If I develop something I prefer to have it accessible for free but not open source.
This allows hobbyists to use it, but prevents companies from ripping off my designs and undercutting development funding through the CaptainBobSim.com/Shop store.
I am considering eventually open-sourcing everything but would like to first be in a financially stable spot.

If you make files you can take a few actions:

- No Action (no file inside folder)
If the contributor takes no action, the folder and subfolders use the default license: https://github.com/CaptainBobSim/The-Cessna-172-Project-V3/blob/main/LICENSE
This means that I can sell these items in my shop (CaptainBobSim.com/shop) to help fund further development.

- Add file "THIS FOLDER IS OPEN SOURCE.MD" inside folder:
If a contributor wants to make their "Open Source", then the unlicense is applied and anyone can use the files for whatever they want.

- Add file "LICENSE NON-COMMERCIAL NO SALES.MD" inside folder:
If you don't want me (or anyone else) to be able to sell it use the "DO NOT SELL"
You may sell things you develop.
If the [project level license](https://github.com/CaptainBobSim/The-Cessna-172-Project-V3/blob/main/LICENSE) is moved to an "OPEN-SOURCE" state (ie. all files are open source), then this folder and subfolders disregard the "NO SALES" constraint (anyone can sell it)
Use this license if you don't want to see items you design in the CaptainBobSim.com/shop store.

Contributors may only add files if they are the primary contributor.
If Captain Bob designs something, and a contributor you change it slightly you aren't allowed to "Open-Source" the design.

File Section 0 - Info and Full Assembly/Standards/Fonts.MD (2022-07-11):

All Panels are done in HELVETICA font (Always bolded).
For me ARIAL is a close second.

Helvetica Font: https://freefontsfamily.com/helvetica-font-family/

Other notable aircraft fonts are 
News Gothic Font: https://fontsgeek.com/fonts/News-Gothic-Regular
Bahnschrift Font: https://fontsgeek.com/bahnschrift-font
MS 33558 Regular font (Standard millitary font): https://www.wfonts.com/font/ms-33558
Calibri
Latha font
Gordon Medium
AV Semi round straight
Futura
Gill Sans

B612 Font (for Avionics Displays ie Airbus): https://b612-font.com/

Specific components:
Turn Coordinator uses Universal Bold: https://fontsgeek.com/fonts/Universal-Bold

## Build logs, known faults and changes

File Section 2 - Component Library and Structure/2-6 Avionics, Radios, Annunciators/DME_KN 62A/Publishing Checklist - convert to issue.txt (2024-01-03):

Design Issues:
- [ ] Add Alignment nubs to parts that have decals

Decals:
- [ ] Decals Printer Friendly Version
- [ ] Laser Engraving Friendly Version

PCB Checklist
- [ ] Ground Plane on bottom
- [ ] "Stay Spicy ✈" airplane :)
- [ ] Autoroute Traces
- [ ] Write Version Number on PCB
- [ ] CaptainBobSim.com
- [ ] Write all component names and Pins

Prototype Issues:
- [ ] 

Publishing Tasks:
- [ ] Add Wiring diagram PNG (Also add to video)
- [ ] Partslist on ReadMe (Also add to video)
- [ ] Rotate and export all STLs using Prusa for easy printability (no slicer rotate)
- [ ] Mounting Template .DXF and maybe PDF
- [ ] Attach .STEP and .f3d
- [ ] MobiFlight .mfmc file
- [ ] FS2020 Mobi .mcc
- [ ] X-Plane Mobi .mcc
- [ ] Take pictures
- [ ] Printables https://www.printables.com/model/create
The Printables version will not be updated. The best place to get it is here: https://captainbobsim.com/product/the-cessna-172-project-files/?customize_changeset_uuid=
Find the MobiFlight code under Section 2/Instrument
- [ ] Tweak the ReadMe
	- [ ] Video Here
	- [ ] Buy it as a Kit/Assembled
	- [ ] Download only this folder via: https://download-directory.github.io/
	- [ ] Pinout?
- [ ] Follow steps on product central https://www.notion.so/captainbobsim/Product-Central-fe05d96d32074a269806f0e77462978f
- [ ] Thumbnail for Video
- [ ] Add links to video

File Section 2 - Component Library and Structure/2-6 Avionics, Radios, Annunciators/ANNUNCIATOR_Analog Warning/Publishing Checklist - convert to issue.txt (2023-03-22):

Design Issues:
- [ ] Decals
- [ ] Engrave version of decals

Prototype Issues:
- [ ] 

Publishing Tasks:
- [ ] Add a DRAWING PDF (optional)
- [ ] Make a Cut/Engrave SVG
- [ ] Rotate all STLs using MeshMixer for easy printability (no slicer rotate)
- [ ] Attach .STEP and .f3d
- [ ] MobiFlight .mcc file and .mfmcfile
- [ ] Mounting Template .DXF
- [ ] Add Wiring diagram PNG
- [ ] Write the ReadMe
	- [ ] Video Here
	- [ ] Buy it as a Kit
	- [ ] Buy it assembled
- [ ] Partslist on ReadMe

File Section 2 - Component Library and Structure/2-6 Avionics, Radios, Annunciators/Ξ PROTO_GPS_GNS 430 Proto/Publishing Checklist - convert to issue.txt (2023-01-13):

Design Issues:

- [ ] Decals
- [ ] 

Prototype Issues:

- [ ] 

Publishing Tasks:

- [ ] Add a DRAWING PDF
- [ ] Attach .STEP and .f3d
- [ ] MobiFlight mcc file
- [ ] Mounting Template .DXF
- [ ] Add Wiring diagram PNG
- [ ] Put fritzing in source
- [ ] Write the ReadMe
	- [ ] Video Here
	- [ ] Buy it as a Kit
	- [ ] Buy it assembled
- [ ] Partslist on ReadMe

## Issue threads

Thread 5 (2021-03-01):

1-1-103 Rib Sliver at 3 o clock

CaptainBobSim, 2021-03-01:
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

CaptainBobSim, 2021-06-18:
Fixed with extrude cut

Closed 2021-06-18.

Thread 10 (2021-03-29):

Fix Stringer Holes 1-1-103 at 3 o clock

CaptainBobSim, 2021-03-29:

Closed 2021-06-18.

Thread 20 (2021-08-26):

Growing pains 1-1-000

CaptainBobSim, 2021-08-26:
When the C172 got fat it grew out of it's clothes and does not fit into them any more.
Since we grew the C172 105% it's original size, some of Section 1's materials are a little out of wack:
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

CaptainBobSim, 2021-12-11:
Issue fixed, will work but not perfect. Will revisit but not urgent (working on section 2 now)

Closed 2021-12-11.

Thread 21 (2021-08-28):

2A Panel Cutout Instrument Knobs

CaptainBobSim, 2021-08-28:
Any instrument with a knob (Altimeter, VSI, HDG, VOR1/2, ADF) has knob cutouts that aren't exactly good.
Altimeter/VSI fit decent, but need adjustment.
VOR, ADF, HDG size needs to be determined.

CaptainBobSim, 2022-01-01:
Fixed during "Breakup CAD Session"
Dang. They shoulda broke up a while ago 🤷‍♀️

Closed 2022-01-01.

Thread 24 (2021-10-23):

2-1-100 sw panel interference

CaptainBobSim, 2021-10-23:
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
Stub interferes with switch panel

CaptainBobSim, 2021-12-11:
Fixed by Vertically constraining edge to dual rocker edge

Closed 2021-12-11.

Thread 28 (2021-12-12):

Rib panel

CaptainBobSim, 2021-12-12:
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

CaptainBobSim, 2022-01-01:
Fixed during "breakup CAD Session"
I'm an emotional wreck 🤷‍♀️

CaptainBobSim, 2022-01-01:
Fixed during "breakup CAD Session"
I'm an emotional wreck 🤷‍♀️

Closed 2022-01-01.

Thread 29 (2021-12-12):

Check the panels upper geometry

CaptainBobSim, 2021-12-12:
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

CaptainBobSim, 2022-01-01:
Fixed! So glad I did it now, and not after 30 million years 🤷‍♀️

Closed 2022-01-01.

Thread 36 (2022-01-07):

Panel is 2" too low

CaptainBobSim, 2022-01-07:
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
Yoke is currently about 23 inches from floor, should be about 25.
Need to check multiple sources to be sure.

CaptainBobSim, 2022-02-09:
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
Moving it creates conflicts - but better now than later!

CaptainBobSim, 2022-02-09:
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
Moved in model still need to go through shell and fix mounting brackets

CaptainBobSim, 2022-02-09:
Redid everything to work with that yoke positioning.
It could have been too high.
The 172 shown was an earlier model, and therefor could be different than the current design.

Closed 2022-02-09.

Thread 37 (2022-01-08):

Instruments Ruined in "Grand Rotation"

CaptainBobSim, 2022-01-08:
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
Need to reorient everything to accommodate a design standard
Airspeed Indicator, Vertical Speed Indicator affected

CaptainBobSim, 2022-01-15:
Instruments given a stern talking too. Issue immediately went away.
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

Closed 2022-01-15.

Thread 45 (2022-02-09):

Missing the bunny ear holes on support structure

CaptainBobSim, 2022-02-09:
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

CaptainBobSim, 2022-02-09:
Bunny ears told to hop into place

Closed 2022-02-09.

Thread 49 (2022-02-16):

CAD mounting holes for Yoke system

CaptainBobSim, 2022-02-16:
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

CaptainBobSim, 2022-03-06:
oops! This is a duplicate, they both got fixed

Closed 2022-03-06.

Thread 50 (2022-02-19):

Yoke linkage arm is too high for ceiling

CaptainBobSim, 2022-02-19:

CaptainBobSim, 2022-03-06:
Mine is just exaggerated 🤷‍♀️
The CAD model is fine

Closed 2022-03-06.

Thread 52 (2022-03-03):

Hole size

CaptainBobSim, 2022-03-03:
Increase mounting hole size from .25 to .3 or .35

CaptainBobSim, 2022-03-06:
hole made bigger, now the removal of panels is easier!

Closed 2022-03-06.

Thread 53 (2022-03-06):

Make yoke mounting holes

CaptainBobSim, 2022-03-06:
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

CaptainBobSim, 2022-03-06:
Holes drilled in the CAD model so that I think we can do them in real life. Such fun!!

CaptainBobSim, 2022-03-06:
Holes drilled in the CAD model so that I think we can do them in real life. Such fun!!

Closed 2022-03-06.

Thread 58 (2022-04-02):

Yoke Issues

CaptainBobSim, 2022-04-02:
POSTPONED - [ ] Yoke Map holder needs to be figured out
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

- [x] Party that I wasn't invited to needs to be fixed

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

- [x] Right lip needs to have upper 2nd piece (to increase modularity)

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

- [x] Cessna Logo needs to be added:

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

- [x] The UnGrommet should be parametrized to the pipe diameter, but everything behind should be at ~1 inch.

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

DECIDED TO POSTPONE- [x] The actual yoke has a carve out making the yoke wiring accessible from the back (still need to decide though.

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

CaptainBobSim, 2022-04-02:
Most items fixed - difficult ones made into separate issues to give ability to work on later (fancy talk for procrastinate)

Closed 2022-04-02.

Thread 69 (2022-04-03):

Redo and wire Switch Panel

CaptainBobSim, 2022-04-03:

CaptainBobSim, 2022-05-12:
Refabricated. Requires wiring.
Issue merged

Closed 2022-05-12.

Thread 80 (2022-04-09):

Fix yoke parts (too weak)

CaptainBobSim, 2022-04-09:
These break easily and pivot around 1 screw
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

CaptainBobSim, 2022-04-24:
Standardized into one Yoke Issue

Closed 2022-04-24.

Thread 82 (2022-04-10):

Fix yoke handle

CaptainBobSim, 2022-04-10:
Yoke handle broke off when dropped on floor.

CaptainBobSim, 2022-04-24:
Reprinted - it was a 3D printer error

Closed 2022-04-24.

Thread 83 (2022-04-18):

Lower Map Box Tolerance

CaptainBobSim, 2022-04-18:
Map box is loose for 3mm material

Closed 2022-04-24.

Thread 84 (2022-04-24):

TaskList for Simulator Display

CaptainBobSim, 2022-04-24:
I'm showing off my simulator at school and Graduation Party
- [x] Switch Panel Fab

Still need to:
- [x] Switch Panel Wire
- [x] Switch Panel Config
- [x] Flaps config
- [x] Replace right slider
- [x] Flaps Glue and Wire
- [x] Glovebox cutout and mount
- [x] Yoke structure
- [x] Air Manager MIP Setup
- [x] Bring computer
- [x] Control Axis Configure

Non Mission Critical:
- [x] Yoke strengthen brackets
- [x] Compass Config

CaptainBobSim, 2022-06-03:
Done! They loved it!

Closed 2022-06-03.

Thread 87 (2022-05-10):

Redesign Roll Mount

CaptainBobSim, 2022-05-10:
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

CaptainBobSim, 2022-05-12:
Slightly redesigned. We'll see how it goes Captain!

Closed 2022-05-12.

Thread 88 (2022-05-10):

Tasks for bottom CNC Part

CaptainBobSim, 2022-05-10:
Before Milling
- [x] Drawer slider pilot holes
- [x] Holes for pillow blocks
- [x] Add Fillet to roll linkage arm (smoother)
- [x] End Stop Holes (multiple for adjustable)
- [x] Mounting holes for a power strip
- [x] Have mounting holes on both yoke part and map box structure.
- [x] TOOLPATH

After Milling:
- [x] Print New Pitch pinion bracket (strengthen)
- [x] Move roll gear out as to not bump
- [x] 90 degree pot mount holes
- [ ] Arduino mounts? (Top part only) mega but possible for uno?
- [x] 90 degree pot mounts should have little holes to stop rotation of pot

Closed 2022-05-18.

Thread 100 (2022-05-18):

Install Avionics Fan [Issue #100 🎉🎉]

CaptainBobSim, 2022-05-18:
We're hooking it up to avionics switches then plugging in an override switch upstream
AV Bus 1:
- TO HSI & GYRO (5)
- TO AUTO-PILOT(4,5)
- TO TRANSPONDER
- TO ADF (2,3,4)
- TO NAV/COM2(2,3,4,5) Speaker power, marker beacon receiver

AV Bus2:
- TO AVIONICS FAN
- TO GPS (2,3,4,5)
- TO NAV/COM1 Headset power, speaker power, marker beacon receiver
- TO AUTOPILOT
- TO ADF

1) BASE
(2) NAVI
(3) NAVII
(4) NAV II WITH 2-AXIS AP
(5) NAV II WITH HSI (1-AXIS OR 2-AXIS AP)

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

CaptainBobSim, 2023-11-01:
Done! Probably won't be a video on it

Closed 2023-11-01.

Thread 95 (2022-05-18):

Fix all CNC mounting holes

CaptainBobSim, 2022-05-18:
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

CaptainBobSim, 2022-09-05:
I think I mighta fixed this?

Closed 2022-09-05.

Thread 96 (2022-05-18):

Tighten tolerances a little bit?

CaptainBobSim, 2022-05-18:
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

CaptainBobSim, 2022-06-03:
We did it!~ We tightened the tolerances!!!!!!!!! 💃🎉🎈🎊🥳🥳🥳🥳🥳🎈🎈🎈🎈

Closed 2022-06-03.

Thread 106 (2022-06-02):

Create Throttle

CaptainBobSim, 2022-06-02:
Design Requirements:

- [x] Must have actual aircraft travel (___mm)
- [x] Should rotate around axis as real one does
- [x] Must use slide potentiometers
- [x] Must be fully 3D Printable, but able to machine?

CaptainBobSim, 2022-06-24:
Done!

Closed 2022-06-24.

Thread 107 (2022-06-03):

Switch panel should be re-dimensioned with fixed constraints.

CaptainBobSim, 2022-06-03:

CaptainBobSim, 2022-06-04:
Basically fixed. Will complete during switch panel redesign

Closed 2022-06-04.

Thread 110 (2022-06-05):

Make the x27 stepper motor backlightable

CaptainBobSim, 2022-06-05:
#109 Added support for LED backlighting. I'd love to add this to the x27 version too!

CaptainBobSim, 2022-09-05:
No longer a priority?

Closed 2022-09-05.

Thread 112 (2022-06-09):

Mark 1 Radio

CaptainBobSim, 2022-06-09:
Design Issues:
- [x] Add Alignment nubs to parts that have decals

Decals:
- [ ] Decals Printer Friendly Version
- [ ] Laser Engraving Friendly Version

Publishing Tasks:
- [x] Add Wiring diagram PNG (Also add to video)
- [x] Partslist on ReadMe (Also add to video)
- [ ] Rotate and export all STLs using Prusa for easy printability (no slicer rotate)
- [ ] Mounting Template .DXF and maybe PDF
- [x] Attach .STEP and .f3d
- [x] MobiFlight .mfmc file
- [x] FS2020 Mobi .mcc
- [x] X-Plane Mobi .mcc
- [x] Take pictures
- [x] Printables
The Printables version will not be updated. The best place to get it is here: https://captainbobsim.com/product/the-cessna-172-project-files/?customize_changeset_uuid=
Find the MobiFlight code under Section 2/Instrument
- [ ] Tweak the ReadMe
	- [x] Video Here
	- [ ] Buy it as a Kit/Assembled
	- [ ] Download only this folder via: https://download-directory.github.io/
	- [x] Pinout?
- [x] Follow steps on product central https://www.notion.so/captainbobsim/Product-Central-fe05d96d32074a269806f0e77462978f
- [x] Thumbnail for Video
- [ ] Add links to video

Modify version for propwash buttons.
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

Closed 2023-07-12.

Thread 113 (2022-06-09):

Increase resolution of Airspeed .MCC

CaptainBobSim, 2022-06-09:
Awesome vid! Very informative and entertaining to watch! Also thanks for mentioning me on the channel! One small note. If you notice your airspeed indicator is choppy or stuttering and not smooth like in the sim you can increase the resolution. Mobiflight rounds up to the nearest integer so it only moves the stepper when going from let’s say 75 to 76 knots. When doing fine maneuvering this stutter is very noticeable. To fix it change your transform to $*10 so the resolution is now 1/10 of a knot. Of course your will need to add a zero to all values in your interpolation table as well. This will make it butter smooth!!!

CaptainBobSim, 2023-01-05:
Done!

Closed 2023-01-05.

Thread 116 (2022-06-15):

Pedestal height and fixes

CaptainBobSim, 2022-06-15:
Add little lip to pedestal and make it easy to cut off the bottom

Make height parametric so you can use a measuring tape

CaptainBobSim, 2022-06-18:
Duplicate

Closed 2022-06-18.

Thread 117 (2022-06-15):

Pedestal height and fixes

CaptainBobSim, 2022-06-15:
- [x] Add little lip to pedestal and make it easy to cut off the bottom

- [x] Make height parametric so you can use a measuring tape

CaptainBobSim, 2022-09-05:
Consider the height parametrized!

Closed 2022-09-05.

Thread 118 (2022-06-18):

Trim wheel should use slip type clutch to promote motorization

CaptainBobSim, 2022-06-18:

CaptainBobSim, 2022-12-16:
Duplicate of #145

Closed 2022-12-16.

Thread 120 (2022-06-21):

Circuit breaker panel doesn't fit I guess?

CaptainBobSim, 2022-06-21:

CaptainBobSim, 2022-11-02:
Fixed

Closed 2022-11-02.

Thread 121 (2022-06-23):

Fix Annunciator PCB

CaptainBobSim, 2022-06-23:
redesign PCB - 9 and 10 both show 9.
Last digit doesn't line up. Need more LEDs. Include switch? Label R/Y for color

CaptainBobSim, 2022-06-24:
LEDs are not added to allow double-sided PCB MFG, to make it more accessible to most.
I like the results I'm getting with the current amount of LEDs

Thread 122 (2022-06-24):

Annunciator PCB Potential Fixes

CaptainBobSim, 2022-06-24:
As an observation, I would usually illuminate an LED by sinking current to ground rather than sourcing current from the microcontroller.   That means bringing the supply voltage to the board with it going to all the resistors, then with each resistor connected to their respective LED’s anode.   Each LED cathode returning to a specific connector pin.   The reason for doing it this way is that it keeps the LED switching current off the micro-P power rails and voltage changes caused by it.  (Ground is usually beefier within the chip as it is the voltage reference for everything inside). Also the n-channel transistors in the uP are typically slightly more conductive than the p-channel transistors on the voltage side.

Of course wiring it this way makes the polarity for the light to be become  “backward” … a “0” lights the LED while a “1” turns it off.

--Arduino Mega has Internal Pullups enabled so not an issue -- I’d also recommend a 10K pullup on each leg of the switch.    … which all depends on what you are connecting the switch to and how that microprocessors I/O is configured.   Even with an Arduino Mega, a pullup should be used.

CaptainBobSim, 2022-07-10:
Due to limitations, this will likely be implemented

CaptainBobSim, 2023-01-07:
4 year old language:
Instead of going

one side to GND one to Pin
go
one side to VCC one to Pin

CaptainBobSim, 2023-03-07:
Shelved to make it more "beginner friendly"

Closed 2023-03-07.

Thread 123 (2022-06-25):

increase loosetol on yoke to .5mm

CaptainBobSim, 2022-06-25:

CaptainBobSim, 2022-09-05:
Ithinkidid?

Closed 2022-09-05.

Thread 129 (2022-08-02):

Mark 2 Flaps

CaptainBobSim, 2022-08-02:
Is it possible to increase the force required to raise / lower the flap lever? It's not a huge deal, it just seems to move up / down with just a fingertip.

- [x] Rotate the servo 180 degrees to save material (longer needle shorter standoff)
- [x] Fix Handle Chamfer
- [ ] Make servo tighter fit (half press fit)

CaptainBobSim, 2023-03-01:
Raise/Adjustable Flaps Resistance

Closed 2023-04-02.

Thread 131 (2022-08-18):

Add lettering to structure mfg model

CaptainBobSim, 2022-08-18:
If you CNC the parts, It should also CNC labels for all of the structure parts

CaptainBobSim, 2022-09-05:
15mm height
2mm cut depth
Ideally Unobtrusive (ie not visible from where seated)

dylanw20141, 2022-09-05:
Took way tooooooooo long but it now looks dank!

Closed 2022-09-05.

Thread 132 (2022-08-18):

Breakers sometimes snap when tightened

CaptainBobSim, 2022-08-18:

CaptainBobSim, 2022-11-02:
Fixed like a boss!

Closed 2022-11-02.

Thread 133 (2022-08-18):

the plastic panel is brittle and if stressed (over tightened) it will break.

CaptainBobSim, 2022-08-18:

CaptainBobSim, 2024-01-27:
This is a known weakness with acrylic. It is a fragile material. In the future I would like to move to metal but the CNC laser is $100,000...

Closed 2024-01-27.

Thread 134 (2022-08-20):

Location of Indicators?

Kovinator, 2022-08-20:
Indicators or instruments like turn coordinator are in section 2A while airspeed indicator and generic are in section 2. Section 2 is titled an instrument section while section 2 says the analog panel.  I don't know if this is intentional or not but I would think it would make more sense to have all the analog dial indicators aka steam gauges  (both small and large) be in one folder and the rest like throttle flaps etc in the analog panel folder.  Your thoughts? Btw I have another pull request coming soon - my focus has been on the support for the  LED lighting to all instruments as well as the 28BYJ stepper motor but would like some clarification as to where these should be located before I contribute. Thanks!

CaptainBobSim, 2022-08-21:
I have these in separate folders because Section 2 is all of the shared components (Airspeed Indicator, Structure and Flaps are the same parts between the G1000 model and the analog model). Right now I only have an analog model so this doesn't make sense, but I have G1000 plans in the future.

What are your thoughts with this?
Is there a better way to do it?

I think your idea of having all steam gauges in one folder is awesome. Where do you think this should go?

Kovinator, 2022-08-21:
Ok, that makes sense. Thanks for the quick reply and clarification! My thoughts on this:

**Option 1:** Leave the current structure as is and simply update the "What Does Each Section Mean?" under the code section.

**Option 2:** Leave the current structure as is and just rename a couple of folders. Ex:

Section 2 - Glareshield and Shared Instruments (G1000 and Analog)
Section 2A - Analog Panel and Instruments
Section 2G - G1000 Panel and Instruments

**Option 3:** Change the directory structure to combine and simplify:

Section 2 Glareshield and Panels
Section 3 Instruments
Section 4 Controls
Section 5 Electronics

With this structure, everything is combined and clearly defined. When going into each section people should be able to figure out what goes on what.

For example, in section 3 the turn coordinator or heading indicator is only on the analog panel.  Note there are only three instruments that are actually shared between the G1000 and analog: The Altimeter, Vertical Speed, and Attitude indicators. Everything else is on the Garmin.

Section 4 would have the physical hands-on controls  (flaps, throttle, yoke, switch panels, etc).

Section 5 electronics. Again the idea here is people can figure out what goes where (Radio Stack equipment on analog, G1000 on the Garmin Panel, annunciator panel on analog, etc. You get the idea.

It's your call how you want to proceed and now that I think about it if you decide to make changes I should commit my changes first while our directory structures are the same that way there are no conflicts. Let me know thanks again!

CaptainBobSim, 2022-08-23:
I decided to go with a mix of all three

I mostly adopted option 3, but with different names.

Section 2 refers to the space on the floor being taken up, so I named the folders 2-(number)-XXX for the level of organization.

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

If you have any improved names for any folders, don't be afraid to shout them out!

Kovinator, 2022-08-25:
I like the great rename! I didn't mean to create more work for you. I was happy with the clarification you gave but man, with what you've done it's much cleaner now! I really like how you did your own combination by adding an extra level of abstraction with section 2 being simply called components and with everything under that being broken down into the appropriate sub-components. Nicely done!

CaptainBobSim, 2022-08-26:
Not extra work! Less work! Better to do it now than when everything is populated.
Thank you for sharing your ideas! I like this system much better :)

Closed 2022-08-25.

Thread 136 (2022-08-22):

Make screws to hold instruments together M3

CaptainBobSim, 2022-08-22:
Everyone hates M2 screws, including myself!
Although they are more realistic, they are kinda terrible.

CaptainBobSim, 2023-01-05:
Hole increased to 3mm
Decrease it to 2.8mm for threading.

CaptainBobSim, 2023-01-05:
Fixed!

Closed 2023-01-05.

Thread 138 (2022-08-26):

Switch Panel is Disassembled

CaptainBobSim, 2022-08-26:
Switch Panel is in pieces...
It needs to be assembled

CaptainBobSim, 2023-05-12:
Put together, except for parts we're redesigning (as a separate issue)

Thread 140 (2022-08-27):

Fix the yoke ungrommet

CaptainBobSim, 2022-08-27:
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
Make a dovetail type joint so there is not a weak point

CaptainBobSim, 2022-09-03:
Dovetail is infeasible

Closed 2022-09-03.

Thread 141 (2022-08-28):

Starter Key Switch needs larger hole

CaptainBobSim, 2022-08-28:

CaptainBobSim, 2022-08-28:
The part split into two parts along the hole for the screw. I suspect that the hole for the screw may be too small.

CaptainBobSim, 2022-09-05:
Fixed, increased .1mm

Closed 2022-09-05.

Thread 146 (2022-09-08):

Design Fuel Instruments

CaptainBobSim, 2022-09-08:

CaptainBobSim, 2022-09-20:
@Kovinator took care of this one!
Might also adjust it for x27 steppers.
Excellent work!

Kovinator, 2022-09-21:
Yep steppers would be cool! The more options we have as sim builders the better! One thing that’s hard to tell are the left right panels behind the glass or in front of it ? I designed it so the panels go behind the glass. I think it looks good that way but not sure if that’s accurate.

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

CaptainBobSim, 2022-10-09:
Hello Kovinator!
Could you send an email to CaptainBobSim@gmail.com with your Fusion 360 username (email) so I can share the team access with you?

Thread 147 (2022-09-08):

Lighting Dual Dimmer

CaptainBobSim, 2022-09-08:
Prototype Issues:
- [x] Put all walls into 2 pieces for simplicity
- [x] Maybe make the knobs fit into Flight Sim Maker Standard?
- [ ] Dimmer knob should be updated for publishing
- [ ] Update Panel cutout 30x40

Publishing Tasks:
- [ ] Add a DRAWING PDF (optional)
- [ ] Rotate and export all STLs using Prusa for easy printability (no slicer rotate)
- [ ] Attach .STEP and .f3d
- [ ] MobiFlight .mcc file and .mfmcfile
- [ ] Mounting Template .DXF
- [ ] Add Wiring diagram PNG
- [ ] Write the ReadMe
	- [ ] Video Here
	- [ ] Buy it as a Kit
	- [ ] Buy it assembled
- [ ] Partslist on ReadMe

CaptainBobSim, 2023-01-10:
Make a dual potentiometer concentric rheostat knob

Closed 2023-12-31.

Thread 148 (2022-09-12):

Support Panel should have a slot for the arduino to fit if glued to the switch panel.

CaptainBobSim, 2022-09-12:
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

CaptainBobSim, 2022-12-16:
Completed ish needs space for cord.

CaptainBobSim, 2022-12-16:
Access granted. If need be, use 90-degree bracket.

Closed 2022-12-16.

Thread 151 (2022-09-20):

Up next

CaptainBobSim, 2022-09-20:
This list is now here: https://github.com/users/CaptainBobSim/projects/2

CaptainBobSim, 2023-01-10:
Just in case. Hehe

For the analog panel only (G1000 is a different animal)
This is for the design of new parts only - fixing old parts is handled under projects/internally
- [x] Means that this has been DESIGNED. Not that it's flawless.
- [x] Challenge LCD Module
- [x] HDG
- [x] Annunciator
- [x] Throttle
- [x] Turn Coord
- [x] VSI
- [x] ALT #176 @CaptainBobSim
- [x] Fuel selector
- [x] Attitude @CaptainBobSim #181
- [x] ADF
- [x] Alt Static
- [x] Parking Brake @CaptainBobSim
- [x] XPNDR @CaptainBobSim
- [ ] VOR/CDI 2
- [ ] GNS 530 @CaptainBobSim
- [ ] Davtron Clock/OAT reserved by @Kovinator
- [ ] VOR/CDI 1
- [ ] Audio Panel
- [ ] Trim Wheel (motorized) @dylanw20141 (but lmk if ya get stuck) #145
- [ ] Brightness knobs @FlightSimClub
- [ ] GNS 430 @CaptainBobSim
- [ ] Mixture #114
- [ ] Heat/Air
- [ ] KR 87 ADF Radio Stack Thing
- [ ] Yoke map light fixes
- [ ] ELT
- [ ] Microphone @FlightSimClub #144
- [ ] Emergency Cutoff
- [ ] Pedestal Lighting and Mic Input
- [ ] Glareshield and lighting
- [ ] KAP 140 Autopilot LCD Version
- [ ] Circuit board for solenoid circuit breakers
- [ ] Rudder Pedals (Static)
- [ ] FFB Yoke
- [ ] FFB Trim (autopilot)
- [ ] FBB Rudder Pedals
- [ ] Real headset interface
- [ ] Enclosure (Sections 1,3,4,5)
- [ ] Fire extinguisher and floor organizer
- [ ] Wiring system for all electronics
- [ ] Lighting system for all components
- [ ] Interior panel work
- [ ] Heating and air
- [ ] Curved projector $$$$$$$$$$$$$$$$$$$$$$$$$$$$$$$$$$$$$$🔥💵💸💰
- [ ] Sheathing?
- [ ] Windshield?
- [ ] V2 Fit-to-stack custom radio
- [ ] V2 KAP 140 Autopilot 7 segment

Closed 2023-01-16.

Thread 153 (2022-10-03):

GPS/NAV Annunciator Fixes

CaptainBobSim, 2022-10-03:
- [ ] GPS ANNUN PCB should have screws on two corners instead of two on top (v2)

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

- [ ] Optional Faceplate cover should be offered

CaptainBobSim, 2022-11-02:
Fixed!

Closed 2022-11-02.

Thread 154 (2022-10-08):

strengthen and redesign arduino mount KASI

CaptainBobSim, 2022-10-08:
Should not protrude beyond instrument for easy removal.
Should be very strong as to not LITERALLY CONSTANTLY BREAK
Trevor. I'm not mad. Just disappointed,

CaptainBobSim, 2023-03-01:
Done #101 #214 #205

Closed 2023-03-01.

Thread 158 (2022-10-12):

Add 4 holes to yoke

CaptainBobSim, 2022-10-12:
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

CaptainBobSim, 2022-10-27:
MFG Problem - not design problem

Closed 2022-10-27.

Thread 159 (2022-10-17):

Put color on LED GPS Annunciator

CaptainBobSim, 2022-10-17:
- [x] Label LEDs by color
- [x] CaptainBobSim text larger
- [x] Change hole position
- [x] MSG via on silkscreen
- [ ] Resistor Value
- [x] Version Number

CaptainBobSim, 2022-11-01:
Resistor value is different for other people :/

Closed 2022-11-01.

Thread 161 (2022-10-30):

GNS 530 Issues

CaptainBobSim, 2022-10-30:
Design Issues:
- [x] Fix Dual Encoders
- [x] RNG Button higher
- [x] Release as single button group
- [x] CDI -> BS - More Height
- [x] Shorten Button slack height
- [x] 3D printed photoresist stand
- [x] Label outgoing and incoming IDC
- [x] 50 vs 47Ω
- [x] LED 13 position
- [ ] Clarify difference
- [ ] re-export circuit board
- [x] CHECK on left push
- [x] Remove the rectangle hole?
- [x] Test photoresistor before ordering new circuit boards!
- [x] Show Backlight
- [x] GNS 530 SD Cards need to be joined
- [x] Adjust heights of buttons and faceplate for holes
- [x] Photoresistor should be not near LED
- [x] Make a mount adapter from big PCB to small PCB 3D printed part. should hold remote buttons
- [x] Fix Com and naV knobs. Actually it's Vloc but naV is more fun in my opinion :D
- [x] More clearance on buttons to avoid sticking
- [x] Photoresistor should be thin
- [x] Make sure there is a hole for the front-facing resistor
- [x] Make clear insert separate from rest of
- [x] give the option for just one part
- [x] Notch in top of Circuit Board for cable relief?
- [x] vertical lid top cover
- [x] Add clearance to SD Cards
- [x] Maybe cover the cable?
- [x] 4 traces are disconnected in LEDs
- [x] dual holes bigger
- [x] Add on new LEDS
- [x] 3 traces are disconnected
- [x] Photoelectric diode
- [x] RNG Button
- [x] Position buttons correctly!!
- [x] PCB
- [x] SHELVED PCB receptacle for both?
- [x] Make GNS 530 have Arduino PCB and OUT IDC and IN IDC
- [x] Make sure 1 actually aligns to 1
- [x] No PCB Outline
- [x] Design Flippy button
- [x] Button Flippy location on PCB
- [x] Put in Zip Tie Cable reliefs
- [x] Single Rotary Encoder Holes in fake backing
- [x] RNG Button Rectangle hole on PCB
- [x] Remove material fro non PCB backing
- [x] Photoelectric sensor just for fun
- [x] Add holes for Display PCB on PCB
- [x] Make silkscreen to ensure IDCs go the correct way
- [x] Dual gns 430 backing 2 options - one for single arduino and one for either GNS 430 or GNS 530 or symmetrical and rotate for other option 🤔 or flip board over?
- [x] Make all buttons rectangle holes?
- [x] Add Alignment nubs to parts that have decals
- [x] Heat Set Inserts

PCB Checklist
- [x] Ground Plane on bottom
- [x] "Stay Spicy ✈" airplane :)
- [x] Autoroute Traces
- [x] Write Version Number on PCB
- [x] CaptainBobSim.com
- [x] Write all component names and Pins
- [x] Write resistor values: 150Ω red 100Ω white (at 5V!) 50Ω for sharing 4 white
- [x] Write Changelog - Top right, size 2.54mm
Changelog
V1.0 Initial Design (Date)

Publishing Tasks:
- [x] Put Partslist in ReadMe Initialize in the BOM (Private) then copy to the ReadMe and video description
- [x] Add Wiring diagram PNG (Also embed in video)
- [x] Rotate and export all STLs using Prusa for easy printability (no slicer rotate)
- [x] Mounting Template .DXF and maybe PDF
- [x] Attach .STEP and .f3d
- [x] MobiFlight .mfmc file
- [x] FS2020 Mobi .mcc
- [ ] X-Plane Mobi .mcc
- [x] Take pictures
- [ ] Printables https://www.printables.com/model/create
The Printables version will not be updated. The best place to get it is here: https://captainbobsim.com/product/the-cessna-172-project-files/?customize_changeset_uuid=
Find the MobiFlight code under Section 2/Instrument
Find BOM in video description.
- [ ] Tweak the ReadMe
	- [x] Video Here
	- [x] Buy it as a Kit/Assembled
	- [ ] Pinout?
- [x] Follow steps on product central https://www.notion.so/captainbobsim/Product-Central-fe05d96d32074a269806f0e77462978f
- [x] Thumbnail for Video
- [x] Add links to video

// - 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

// 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

CaptainBobSim, 2022-10-30:
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

Closed 2024-08-23.

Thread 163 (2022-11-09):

Throttle tol

CaptainBobSim, 2022-11-09:
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

CaptainBobSim, 2022-12-16:
The throttle should loosely fit

CaptainBobSim, 2022-12-16:
Consider it toleranced!

Closed 2022-12-16.

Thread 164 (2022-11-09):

Attitude Indicator Build

CaptainBobSim, 2022-11-09:
Attitude Indicator:
- Must use BYJ48 Stepper Motors
- Must fit into the standard cutout
- Must look similar to authentic Cessna 172
- Must have pitch and roll function.

Should/Nice to Have:
- Zeroing mechanism - Microswitch
- Have an adjustable viewpoint

CaptainBobSim, 2023-01-02:
Good nuff

Closed 2023-01-02.

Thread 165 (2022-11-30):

Keep 'em flying

CaptainBobSim, 2022-11-30:
- [ ] Mixture
- [ ] Trim wheel
- [ ] Key and switch panel
- [ ] Fuel selector

CaptainBobSim, 2022-12-16:
I missed the payment for the involvement expo..........

CaptainBobSim, 2022-12-16:
Duplicate of #151

Closed 2022-12-16.

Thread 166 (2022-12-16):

Heading Indicator Cutout

CaptainBobSim, 2022-12-16:
Technically there are 3 screws on HDG, not just 2.
This is a lot of work though and I've had a rough day.

CaptainBobSim, 2022-12-16:
Still a rough day. but my quotes app said something like "nobody cares about your feelings" and I was like you've got a point.

The third hole exists! Although kinda weird NGL

Closed 2022-12-16.

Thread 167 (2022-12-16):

Psycho-Small Issues

CaptainBobSim, 2022-12-16:
- [x] 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
- [x] Holes are too big for instrument screws
- [x] These are straight, not curvy
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
- [x] little "imperfection" needs enlarging 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

CaptainBobSim, 2022-12-16:
Fixed! better a pebble without a flaw than a diamond with!

Closed 2022-12-16.

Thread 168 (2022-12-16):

Fit Small Kovinator Instruments into C172 Project

CaptainBobSim, 2022-12-16:
Kovinator made awesome instruments! Now I just need to fit them into the project

CaptainBobSim, 2022-12-29:
These look really spiffy @Kovinator
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

Kovinator, 2023-01-01:
Happy New Year!!!!!

Here are some pics of the small instrument using the junction box.

[image: image2.jpeg]

Need to paint the EGT needle but which color red or yellow?

[image: image1.jpeg]
Here is a picture from the top.

[image: image3.jpeg]

Here is from the side. I cut off all the extra servo wire and crimped on
dupont connectors to keep
things nice and clean. LEDs have resistor soldered in with the harness.

[image: image0.jpeg]

Time for a night flight. I may switch to yellow instead of white. What
color are you going to use? I also added a POT so I can dim them using PWM
in mobiflight.

On Thu, Dec 29, 2022 at 1:16 PM Trevor Olsen ***@***.***>
wrote:

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

CaptainBobSim, 2023-01-01:
Did the images attach correctly? I don't know if they do when using email.

CaptainBobSim, 2023-01-01:
I think yellow might be better for the EGT gauge.
I'm using white lighting for all instruments, but that's just what I've been throwing in. Which do you think is more realistic?
For me I'm having everything on an external dimming piece of hardware.

Closed 2022-12-29.

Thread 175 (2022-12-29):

Heading Indicator Issues

CaptainBobSim, 2022-12-29:
Design Issues:
- [x] Ring gear is still tight tolerance :/
- [x] Bigger Gear
- [x] Thicc Gear wheel
- [x] Wheel has mag
- [x] Mag opposite bug
- [x] Hall Sensor for Bug
- [x] Knobs are too tight
- [x] Square shaft for knobs
- [x] Redo encoder holes
- [x] inc backing to 3mm
- [x] Thicken the hdg bug thingies.
- [x] Hall effect housing (Especially bug)
- [x] hole to remove magnet
- [x] Fake lil demon dot needs alignment (see image below)
- [x] Decals
- [x] Make a little tick little airplane for engrave airplane version
- [x] Make an engraved airplane SVG
- [x] Upload blank knobs and update decal.
- [x] Add all links to youtube video :)
- [x] HDG Decal needs Margins oops

PCB Issues:
- [x] Add a slot for pushing motor connectors through
- [x] Silk Screening for item positioning
- [x] Figure out encoder positioning
- [x] Swap Connector Direction on PCB
- [x] +and - on PCB (- is connected to ground) for external power supply
- [x] Rotate this around!
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
- [x] I did a big oopsies with the motor configuration on the PCB
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

Publishing Tasks:
- [x] Add a DRAWING PDF
- [x] Attach .STEP and .f3d
- [x] MobiFlight mcc file
- [x] Mounting Template .DXF
- [x] Add Wiring diagram PNG
- [x] Put fritzing in source
- [x] Write the ReadMe
	- [x] Video Here
	- [x] Buy it as a Kit
	- [x] Buy it assembled
- [x] Partslist on ReadMe

little fake demon dot needs alignment
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

CaptainBobSim, 2023-01-27:
Archived: 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

CaptainBobSim, 2023-02-28:
WE DID IT EVERYONE!!! WE FINISHED THE HEADING INDICATOR!!

Closed 2023-02-28.

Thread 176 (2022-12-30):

Altimetissues

CaptainBobSim, 2022-12-30:
Design Issues:
- [x] make the needles have a flat spot where you can mount onto it without turning, kinda like the byjs have (similar to a square drive)
- [x] Decals
- [x] Engrave version of decals
- [x] Add hand modification for the people who are like "That's not MY altimeter MINE HAS PRETTY HAND!"
- [x] Make a big hole where the big hole goes altimeter (what the heck do you mean trevor like seriously) -- potentiometer hole make sure big enough.
- [x] Decal add center holes (non-intrusive) -- shelved because the outline helps you align it now --
- [x] Spacing between pillar and gear knob
- [x] One of the stepper gears needs to have a hole put in it (that's not supposed to be a threat)
- [x] The 100 ft hand looks dumb and stupid and dumb
- [x] widen encoder shaft holes
- [x] Altimeter gears are actually too loose!
- [x] Save plastic on stepper holder assy
- [x] Screw that! The screws just went "I'mma head out" [my progress deleted]
- [x] Allow the potentiometer to be on both sides
- [x] needles protrude through the glass. oof
- [x] Things keep breaking off of gears and hands
- [x] Make gears module lower (m=1)
- [x] Make Decals 🤮
- [x] direct drive 100 ft hand coupler
- [x] Add 100 1K 10K markings on gears
- [x] Make Decals for hands
- [x] Coupler tolerance needs to be larger
- [x] Coupler needs to have thicker diameter
- [x] Make gears 1-2mm shorter
- [x] Add the left window? metricy
- [x] Fix lighting
- [x] Gear/Needle gap needs to be smaller
- [x] Standoff near adjust knob
- [x] Make 10Turn Pot Hole correct size
- [x] Make a gap for backing (cord?)
- [x] Loosen shaft tightness
- [x] Make a hole for header 10K
- [x] Coupler Biggen
- [x] Square Shaft
- [x] Screw goes into gear when attaching to panel (give it more slack:?)
- [x] Add "adjustment screw" north of the knob
- [x] Make sure shafts are all perfectly concentric

Other Issues:
- [x] Coupler needs square shaft
- [x] Lighting Conflict with Altimeter #177
- [x] Woops 10,000 ft barber pole arch went bye bye
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

Publishing Tasks:
- [x] Add a DRAWING PDF (optional)
- [x] Make a Cut/Engrave SVG
- [x] Rotate all STLs using MeshMixer for easy printability (no slicer rotate)
- [x] Attach .STEP and .f3d
- [x] MobiFlight .mcc file and .mfmcfile
- [x] Mounting Template .DXF
- [x] Add Wiring diagram PNG
- [x] Write the ReadMe
	- [x] Video Here
	- [x] Buy it as a Kit
	- [x] Buy it assembled
- [x] Partslist on ReadMe
- [x] Download only this folder via: https://download-directory.github.io/

CaptainBobSim, 2023-05-12:
Closed! Video scheduled, available to patreons.

Closed 2023-05-12.

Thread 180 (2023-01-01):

Templates

CaptainBobSim, 2023-01-01:
- [x] Drawings
- [x] Decals
- [x] Folder structure
- [ ] Video assets
- [x] Mounting Things
- [x] Instructions
- [x] BOM

CaptainBobSim, 2023-01-10:
Good enough! I'll work on assets on my own.

Closed 2023-01-10.

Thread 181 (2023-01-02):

Watch your Attitude! Attitude Issues

CaptainBobSim, 2023-01-02:
PROTOTYPE/TESTING ISSUES
- [x] Add alignment nubs
- [x] Bezel bottom square should be "fleshed out"
- [x] Expand slot on attitude backing so wires can easily fit through
- [x] Have an adjustable viewpoint
- [x] Move zero(s) to bottom
- [x] Cut the back circle into a square
- [x] Move zero microswitches down
- [x] Build up material next to pitch motor mount
- [x] make the roll cover circle (no nubs)
- [x] ensure runaway situation won't break instrument
- [x] put in a nut capturator 3000 so that attitude can get screwed into panel
- [x] Conflicts with pillars
- [x] Inc distance between pitch arm and base
- [x] Knurl Knobs
- [x] Fix the lighting issue I made when I overrode the bezel
- [x] Pitch arm now touches roll body
- [x] Finish Fixing bezel - it should be bigger which fixes the pillar issue
- [x] Fillet the base to circle and fillet to add strength (kinda)

DESIGN ISSUES
- [x] Add microswitches to hard stop.
- [x] Make decals 🤮
- [x] microswitch idea pitch
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
- [x] Little attitude bug
- [x] Little airplane :)
- [x] Attach bank wheel to spiny doohicky
- [x] Seal Conflict
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
- [x] When attitude goes too far pitch up it intersects - change center point of radii to be the same.
- [x] Attach bezel to back piece
- [x] Glass has "Vacuum" word. ---DECAL IS FAIR COMPROMISE---
- [x] Gyro flag? ---FAIR COMPROMISE---
- [x] Little screws on decals --- Didn't look great!---
- [x] Redo decals for "no numbers" version

From #164
Attitude Indicator:
- [x] Must use BYJ48 Stepper Motors
- [x] Must fit into the standard cutout
- [x] Must look similar to authentic Cessna 172
- [x] Must have pitch and roll function.

Should/Nice to Have:
- [x] Zeroing mechanism - Microswitch

- [x] No bueno
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

Design Issues:
- [x] Decals
- [x] Engrave version of decals
- [x] Add Alignment nubs to parts that have decals

PCB Checklist -- PCB is put on hold --
- [ ] Ground Plane on bottom
- [ ] Stay Spicy airplane :)
- [ ] Autoroute Traces
- [ ] Write Version Number on PCB
- [ ] CaptainBobSim.com
- [ ] Write all component names

Publishing Tasks:
- [x] Add a DRAWING PDF (optional)
- [x] Make a Cut/Engrave SVG
- [x] Rotate and export all STLs using Prusa for easy printability (no slicer rotate)
- [x] Attach .STEP and .f3d
- [x] MobiFlight .mcc file and .mfmcfile
- [x] Mounting Template .DXF
- [x] Add Wiring diagram PNG
- [x] Write the ReadMe
	- [x] Video Here
	- [x] Buy it as a Kit
	- [x] Buy it assembled
- [x] Partslist on ReadMe
- [x] Download only this folder via: https://download-directory.github.io/
- [x] Follow steps on product central https://www.notion.so/captainbobsim/Product-Central-fe05d96d32074a269806f0e77462978f

CaptainBobSim, 2023-06-02:
FIIIIIIIIIIIIIIIIIIINAAAAAAAAAAAAAAALLAYYYYYYYYYYYYYYYYYY it's done!

Closed 2023-06-02.

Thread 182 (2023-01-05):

I think this one dude wants the display to be behind the panel

CaptainBobSim, 2023-01-05:
Someone wanted a V1 version with the  16x2 behind the panel but I was like nah man that's effort. but now I'm like maybe he's got a point? but mostly I'm like nah man that's effort.
3D print files - V1 Small Multi Radio 16x2

CaptainBobSim, 2023-02-04:
That's a lot of effort.
Respond to this/start new issue if you think otherwise!

Closed 2023-02-04.

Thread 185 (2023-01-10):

From Prototype to Product/Video

CaptainBobSim, 2023-01-10:
@CSU locked me out of my dorm that costs $1200 per month (+$500 for a ridiculous meal plan but that's another story) over winter break
I could just run over and grab components but the ^(&&**&^^%#(#& system is rigged!
- [ ] Tachometer X27
- [ ] VSI
- [ ] ADF
- [ ] CDI 2
- [ ] HDG
- [ ] Attitude
- [ ] Altitude
- [ ] Transponder
- [ ] Radio
- [ ] Parking Brake
- [ ] Alt Static Air

CaptainBobSim, 2023-01-10:
Added to project. Thanks for coming to my Ted talk

Closed 2023-01-10.

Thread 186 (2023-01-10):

KT 76C Transponder Issues

CaptainBobSim, 2023-01-10:
Design Issues:
- [x] Add the slotted slot thing to the side\
- [x] Make decals/engrave files
- [x] Fix the rotary switch nut position (should it be in the sandwich layer?
- [x] Add Alignment nubs to parts that have decals

Prototype Issues:
- [x] Buttons need to be higher
- [x] Tolerance needs to be increased (even though I just decreased it oops)
- [x] Backing needs no holes
- [x] Backing needs to navigate around PCB components
- [x] Wright a "R" and "L" on the Bezel Spacer
- [x] Move hole down before buy new PCBs
- [x] Redo holes and crap?
- [x] Order new PCBs?

Decals:
- [x] Decals Printer Friendly Version
- [x] Laser Engraving Friendly Version

PCB Checklist
- [x] Ground Plane on bottom
- [x] "Stay Spicy ✈" airplane :)
- [x] Autoroute Traces
- [x] Write Version Number on PCB
- [x] CaptainBobSim.com
- [ ] Write all component names and Pins

Publishing Tasks:
- [x] Add Wiring diagram PNG (Also add to video)
- [x] Partslist on ReadMe (Also add to video)
- [x] Rotate and export all STLs using Prusa for easy printability (no slicer rotate)
- [x] Mounting Template .DXF and maybe PDF
- [x] Attach .STEP and .f3d
- [x] MobiFlight .mfmc file
- [x] FS2020 Mobi .mcc
- [ ] X-Plane Mobi .mcc
- [x] Take pictures
- [x] Printables
The Printables version will not be updated. The best place to get it is here: https://captainbobsim.com/product/the-cessna-172-project-files/?customize_changeset_uuid=
Find the MobiFlight code under Section 2/Instrument
- [x] Tweak the ReadMe
	- [x] Video Here
	- [x] Buy it as a Kit/Assembled
	- [x] Download only this folder via: https://download-directory.github.io/
	- [x] Pinout?
- [ ] Follow steps on product central https://www.notion.so/captainbobsim/Product-Central-fe05d96d32074a269806f0e77462978f
- [x] Thumbnail for Video
- [x] Add links to video

Closed 2024-03-15.

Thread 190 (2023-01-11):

Notes

CaptainBobSim, 2023-01-11:
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

CaptainBobSim, 2023-01-16:
* "Sponsor" a design pay x2 as much to aid dev costs
* Export no glue and glue gears .20 and .30 mm
* Attitude use Hall Effect or IR?
* Hall Effect in Heading?
* Download 7 seg library
* Components male, Arduino female?
* Move G1000 Stack up in priority and shared G1000 components
* Standby Panel Product G1000
* Contact Peters for 182 Dimensions
* Hall effect for zeroing CDI
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

CaptainBobSim, 2023-03-02:
Closed

Closed 2023-03-02.

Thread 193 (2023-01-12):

GNS 430 @CaptainBobSim

CaptainBobSim, 2023-01-12:
Design Issues:
- [ ] Decals
- [x] PCB
- [x] SHELVED PCB receptacle for both?
- [x] Make GNS 530 have Arduino PCB and OUT IDC and IN IDC
- [x] Make sure 1 actually aligns to 1
- [x] No PCB Outline
- [x] Design Flippy button
- [ ] Button Flippy location on PCB
- [x] Put in Zip Tie Cable reliefs
- [ ] Single Rotary Encoder Holes in fake backing
- [ ] RNG Button Rectangle hole on PCB
- [ ] Remove material fro non PCB backing
- [ ] Photoelectric sensor just for fun
- [ ] Add holes for Display PCB on PCB
- [ ] Make silkscreen to ensure IDCs go the correct way
- [ ] Look through all complete 530 issues

Prototype Issues:
- [ ] Non PCB XY Define button width

Prototype Issues:
- [ ]

Publishing Tasks:
- [ ] Add a DRAWING PDF
- [ ] Attach .STEP and .f3d
- [ ] MobiFlight mcc file
- [ ] Mounting Template .DXF
- [ ] Add Wiring diagram PNG
- [ ] Put fritzing in source
- [ ] Write the ReadMe
	- [ ] Video Here
	- [ ] Buy it as a Kit
	- [ ] Buy it assembled
- [ ] Partslist on ReadMe

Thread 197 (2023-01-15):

Junction Disfunction is not a function!

Kovinator, 2023-01-15:
I don't know if this is reproducible or something weird I don't understand but the junction boxes I made to consolidate common wires is causing some problems. The issue is that at least for servos I'm seeing what can only be described as feedback jitters.

For example from the sim I can fill the tanks, when I fill the right tank in the sim the left tank goes up and down like crazy really fast even though that tank isn't being modified. If I look at mobiflight I do not see the numbers change for the left just the right so it's not the sim or mobiflight.  If I take the 5v and ground for that servo and plug it into a breadboard instead of the junction the problem goes away.

Have you seen this before? Do you know what is causing it? I wonder if there is RF noise being generated due to the servo wires being really short (only an inch or two). Or maybe it has something to do with junction boxes being too close to the servo?  Maybe it's both? Maybe the current draw is too high and its causing signal drops? (don't have external power supply yet) and I'm driving 4 servos with the Arduino.

Maybe I'm somehow generating an inductive field that will open a gateway to another dimension?

Maybe aliens are trying to speak to me through the servos somehow.  Got any thoughts?

CaptainBobSim, 2023-01-15:
I think the Arduino can provide 500mA via USB, and each servo uses somewhere around 250mA.

Try running the test sketch on motif light which will trigger them each individually vs trying to move them all at once.
Also, consider trying to run just two at a time in your current configuration and see if that changes anything.

I'd also prepare a light snack of various electronics for the aliens - a long voyage might make them power hungry!

Kovinator, 2023-01-15:
Yeah already tried just the two servos. I’ll try your suggestions thanks !On Jan 15, 2023, at 12:37 AM, Trevor Olsen ***@***.***> wrote:
I think the Arduino can provide 500mA via USB, and each servo uses somewhere around 250mA.
Try running the test sketch on motif light which will trigger them each individually vs trying to move them all at once.
Also, consider trying to run just two at a time in your current configuration and see if that changes anything.
I'd also prepare a light snack of various electronics for the aliens - a long voyage might make them power hungry!

—Reply to this email directly, view it on GitHub, or unsubscribe.You are receiving this because you authored the thread.Message ID: ***@***.***>

Kovinator, 2023-01-20:
Update. It seems to be related to the LEDs. Specifically PWM. If the LEDs are on using PWM then the servos seem to go crazy. For example:

LED Transform:
if (1=1,255,0) LEDs ON - NO PROBLEM
if (1=1,0,0) LEDs OFF - NO PROBLEM
if (1=1,128,0) LEDs (50%) Crazy servo moving all over the place not obeying mobiflight.

Pinout:
led pins (5) PWM enabled in mobiflight Note: All LEDs share this pin
LEDs are wired in parallel each having its own 100ohm resistor wired to the cathode.
servo pins (31,33,35,37) are signals for the servos.

Power:
I'm now using an external power source (modded PC power supply). This will go inside the glovebox to power the entire panel. All grounds and voltages are supplied by this power supply to everything using a breadboard.
The Arduino is powered from this power supply through the VIN pin and ground using the same power supply.

Conclusion:
I must have miswired something. I suspect one of the LEDs is to blame. I could have wired it backward? The resistor on positive instead of negative maybe? One of my servos quit working which I'm not sure if is related or not.  I'll keep at it.

Kovinator, 2023-02-21:
There are actually two issues and both now are solved. The servo jitter originally was caused by pulling too much amperage when the Arduino is powered just by USB as Trevor suggested. When using an external power supply to try and fix this the jitters became worse and I assumed this was the same issue but this was actually caused by a separate issue related to incorrect wiring of the external power supply.

Using an external power supply is a must when having a higher load. When using an external power supply I had positive 12v and negative hooked to the power pins on the Arduino which is pretty much the same as plugging it in through the DC jack. This powers the Arduino and allows for more amperage (1 AMP as opposed to 1/2 AMP USB).  Also, it allows me to power servos and step motors directly from the power supply to keep the load on the Arduino as small as possible.

Resolution:
My mistake was grounding the breadboard to the common ground on the power supply. Seemed logical to me at the time but it's not. It allows for different ground potentials. To correct the issue the breadboard needs to be grounded to the Arduino NOT the power supply.

Simple Servo example -  (Breadboard eliminated for simplicity) What I had was this:
Servo Positive - Power Supply +
Servo Negative - Power Supply -
Servo Signal - Arduino Servo Pin (PWM)

I changed it to this:
Servo Positive - Power Supply +
Servo Negative - GND pin on Arduino
Servo Signal - Arduino Servo Pin (PWM)

A simple mistake that took hours to find. Hope this helps someone else. Eventually, I would love to see a step motor design for the smaller instruments but they are too small to put the step motors directly side by side. Eventually, we will get there! I'm glad this is finally closed. Thanks for the help!

CaptainBobSim, 2023-02-23:
I'm glad you could solve this! I will make sure to be careful when wiring ext power supplies.
Thank you for sharing your findings!

Closed 2023-02-21.

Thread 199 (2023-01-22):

1 Standard 6x6 button (not many!)

CaptainBobSim, 2023-01-22:
The PCB by default puts the buttons in a different space than if you do not use a PCB
Behind backing vs in backing piece.
Maybe have one board piece that press fits them in and another that fits around them loosely (like how the annunciator is designed with a "Press fit" LED and a "Loose Fit" LED for the circuit board

CaptainBobSim, 2023-05-12:
Yep Standard created!

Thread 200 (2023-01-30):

Make an Airliner Circuit Breaker G1000 style 🥳Issue #200

CaptainBobSim, 2023-01-30:
I did some crap designing it I just need to change it over to a electromagnet and microswitch

CaptainBobSim, 2023-03-05:
Finished!

Closed 2023-03-05.

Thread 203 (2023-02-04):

VSI

CaptainBobSim, 2023-02-04:
Design Issues:
- [x]  Tweak BYJ Version!
- [x] Make x27 2nd Version Decals
- [x] Decals
- [x] Engrave version of decals

Prototype Issues:
- [ ]

Publishing Tasks:

- [x] Add a DRAWING PDF
- [x] Make a Cut/Engrave SVG
- [x] Attach .STEP and .f3d
- [x] MobiFlight mcc file
- [x] Mounting Template .DXF
- [x] Add Wiring diagram PNG
- [x] Put fritzing in source
- [x] Write the ReadMe
	- [x] Video Here
	- [x] Buy it as a Kit
	- [x] Buy it assembled
- [x] Partslist on ReadMe

CaptainBobSim, 2023-03-22:
Woohoo!

Closed 2023-03-22.

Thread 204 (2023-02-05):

Relay Trigger System

CaptainBobSim, 2023-02-05:
Pop System needs to also have a few extra relay slots for aux things:
- Hobbs Meter
- Avionics Fan

CaptainBobSim, 2023-02-05:
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

CaptainBobSim, 2023-02-05:
Cigarette lighter is the DC Automotive power source - I'm also optionally just replacing those with 5V USB

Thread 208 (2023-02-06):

Make "All Decal Sheets"

CaptainBobSim, 2023-02-06:
Save paper with sheets (Maybe broken up by panel?)
1. 6 Pack
2. 6 Pack
3. 6 Pack
4. Fuel Instruments
5. Nav Instruments
6. Radio A
7. Radio B
8. Radio C
9. Pedestal
10. Switch Panel

CaptainBobSim, 2024-01-27:
Done on panel by panel basis!

Closed 2024-01-27.

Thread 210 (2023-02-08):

Maybe make changes to Switch?

CaptainBobSim, 2023-02-08:
https://www.thingiverse.com/thing:5843297
Summary
This is a remix of [CaptainBobSim's keyswitch](https://www.thingiverse.com/thing:4978867) with inspiration from [AllanGlen's version](https://www.thingiverse.com/thing:2687594).

The goal was to make CaptainBob's keyswitch easier to assemble:

Uses a keyed slot to position the lock body rather than the captive nut, which made it difficult to tighten properly while keeping desired lock alignment
Integrates the metal components from the back of lock (alignment washer, latching tab) into a printable coupler mechanism to reduce the number of small metal parts that need to be held in place during assembly
Materials
Filing Cabinet Lock (amazon, etc)
5-position rotary switch (amazon, etc)

~1.5" x 0.25" diameter extension spring (can accept wide range of springy things, such as rubber bands)
2x ~1cm ~M3 screws (to hold spring)

OpenSCAD source is available on my github and is designed to be parametric so that you can customize it to suit your needs: [Printable parts](https://github.com/chungl/flight-sim/tree/main/c172/components/ignition_keyswitch) and [Panel label SVG](https://github.com/chungl/flight-sim/tree/main/c172/elec_panel)

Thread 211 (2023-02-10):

New Annunciator with only 9-10 pins (v4)

CaptainBobSim, 2023-02-10:
Annunciator only has 9 controllable LEDs therefore should only use 9 pins (not 13)
 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
Two additional pins for TST/DIM makes this 11 (not 15)
+GND for 12 not 16

Other Tasks:
- [x] in series vs parallel LED Annunciator
- [x] Label all pins
- [x] [Shelved] Popout VCC???
- [x] [Shelved - this is so close to the instruments that it doesn't make sense to have it as a standalone unit] I should be able to directly attach a pro micro to the board (ie gnd pops 1 out from the rest of the pins)

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

Closed 2023-05-17.

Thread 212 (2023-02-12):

Decals need to have margins for printing

CaptainBobSim, 2023-02-12:
Woops! I didn't realize printers need a little bitta wiggle room!

CaptainBobSim, 2023-03-07:
I think I accounted for this...

Closed 2023-03-07.

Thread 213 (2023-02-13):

Make x27 PCBs

CaptainBobSim, 2023-02-13:
Task 1:
- [ ] Make footprint (with holes for standoffs and screws)

Use this datasheet for dimensions: https://4tronix.co.uk/zeropoint/x27_spec.pdf
Use this playlist as a guide :) https://youtu.be/NITJZfhjppI

Task 2:
- [ ] Generic PCB for x27
Use the above playlist for inspiration
Should go from pins 1 2 3 4 on custom motor footprint (Task 1) to 1 2 3 4 on a 1x4 pin header (pinhead)
Be careful to make sure back of pin headers don't interfere with motor profile.

Task 3: @CaptainBobSim
- [ ] Dual for Turn Coord

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

CaptainBobSim, 2023-05-16:
Complete!

Closed 2023-05-16.

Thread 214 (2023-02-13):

Instrument Arduino Mount Tweaks

CaptainBobSim, 2023-02-13:
- [x] Should have holes  left and right for wires
- [x] Should have more standoff holes

CaptainBobSim, 2023-02-24:
Yes please! We're done!

Closed 2023-02-24.

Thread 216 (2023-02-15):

Sourcing Push Pull Switch - Make a Standard

CaptainBobSim, 2023-02-15:
HEEY!! I could make a push pull switch with a toggle switch :)

[push pull on off switch for sale | eBay](https://www.ebay.com/sch/i.html?_nkw=push+pull+on+off+switch&_sop=12)
[2 Position ON OFF HeadLight Switch, Push Pull EZGO Club Car Golf Cart Forklift | eBay](https://www.ebay.com/itm/122644967877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)
[Push / Pull Switch Dorman 85955 | eBay](https://www.ebay.com/itm/314174539224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)
[Dorman: 85933 - Push / Pull Switch | eBay](https://www.ebay.com/itm/325295439151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)
[Golf Cart Push Pull Light Switch 12 Volt for Club Car Yamaha EZGO Headlights 12V | eBay](https://www.ebay.com/itm/181844480484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)
[Heavy Duty Push Pull Switch 2 position ON-OFF Chrome Knob and Bezel Nut e | eBay](https://www.ebay.com/itm/301541031698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)
[30 Amp Universal Push-pull Light Switch Niehoff UN18110 | eBay](https://www.ebay.com/itm/185228195545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)
[Long On Off Push Pull Switch 12v 5AMP + Screws Terminals Long Thread Rod | eBay](https://www.ebay.com/itm/283935906429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)
[The Cessna 172 Project Priority List](https://github.com/users/CaptainBobSim/projects/2/views/1?pane=issue&itemId=17721933)

CaptainBobSim, 2023-06-30:
Hooray the standard has been implemented!

Closed 2023-06-30.

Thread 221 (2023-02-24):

Print then Laser

CaptainBobSim, 2023-02-24:
Make the Print on USA Shipping label then cut out with Laser process easy.

Make laser standards (say orange is for paper)

Have a zero dot.

CaptainBobSim, 2023-05-12:
Updated to decal, will have to back implement where needed (but will do as we need)

Closed 2023-05-12.

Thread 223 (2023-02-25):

Flight Sim Club Tasks

CaptainBobSim, 2023-02-25:
Todo:
- [ ] Dimming system, wire + and - to red and black respectively.
- [ ] Make a 4-foot wiring loom with 4 white and 1 black wire. Connect the black wire and white to red pull switch via screws. Strip ~1/4" off.
- [ ] Power distribution
- [ ] Hook up Lighting for pedestal to dimmer
- [ ] G1000 solder
- [ ] Tachometer replace motor with X27 version
- [ ] Tidy wire
- [ ] Fuel instruments
- [ ] Get instruments to work
- [ ] Work out controls in MobiFlight
- [ ] Install Avionics Fan
- [ ] Avionics switch logic
- [ ] play around with FFB
- [ ] work on key?
- [ ] G1000 build circuit board
- [ ] Wire up trim wheel
- [ ] Bass Shaker configure
- [ ] GPS NAV
- [ ] Plan Party

Trevor needs to do some stuff first:
- [ ] solder switch panel circuit board
- [ ] 9V Battery

Claimed:
- [ ]

Completed!
- [x] Assemble flaps
- [x] Choose a motor for Trim Wheel?
- [x] Convert project drafts to issues then complete
- [x] Replace wiring loom with PCB on Heading Indicator
- [x] Install Radio Stack Mounts (The black pieces need to be drilled into the backing panel)

Great First Projects [Reply with your project, and "CLAIMED"]
- Compass
- ELT
- Fuel Selector
- Lower Pedestal Panel
-  Floor Organizer and Fire Extinguisher holder
- [Make a dual switch MASTER that's based on screw instead of glue.](https://github.com/users/CaptainBobSim/projects/2/views/1#)

CaptainBobSim, 2023-04-26:
Now using the project - I'll archive the project over the summer when flightsimclub is not in session

Closed 2023-04-26.

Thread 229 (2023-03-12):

Don't know where to put this...

CaptainBobSim, 2023-03-12:
### Discussed in https://github.com/CaptainBobSim/The-Cessna-172-Project-V3/discussions/225

<div type='discussions-op-text'>

<sup>Originally posted by **geologistluna** February 28, 2023</sup>
I've been going through your project and am quite impressed by it.  Its an amazing feat to have done this to this point, however, I am starting to find small errors. One such error is a mislabeled or duplicate .stl which is confusing.  The specific file I am speaking of is "The-Cessna-172-Project-V3/Section 2 - Component Library and Structure/2-5 Instruments/SMALL_EGT Indicator/9g Servo/STLs/Display Backplate.stl" which appears to be a copy of the file "Servo Motor plate.stl" and "Servo SG90 Horn.stl".

Of course I may be completely wrong, and off my rocker. Thank you! </div>

Closed 2023-03-12.

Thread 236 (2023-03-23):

Put brass inserts in the Yoke

CaptainBobSim, 2023-03-23:
I figured it out! I’ll use brass inserts in the yoke, because it legit really needs them! The holes are long enough that if you don’t have brass inserts you can tap it into the plastic!

CaptainBobSim, 2023-06-28:
duplicate of #60

Closed 2023-06-28.

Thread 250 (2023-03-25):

Parking Brake

CaptainBobSim, 2023-03-25:
Design Issues:
- [ ] Decals
- [ ]

Prototype Issues:
- [ ]

Publishing Tasks:

- [ ] Add a DRAWING PDF
- [ ] Attach .STEP and .f3d
- [ ] MobiFlight mcc file
- [ ] Mounting Template .DXF
- [ ] Add Wiring diagram PNG
- [ ] Put fritzing in source
- [ ] Write the ReadMe
	- [ ] Video Here
	- [ ] Buy it as a Kit
	- [ ] Buy it assembled
- [ ] Partslist on ReadMe

CaptainBobSim, 2023-04-28:
Issue closed, not really in development rn

Closed 2023-04-28.

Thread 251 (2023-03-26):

Change back to M2 Screws - I miss them

CaptainBobSim, 2023-03-26:
for panel screws

Well now I'm having a debate!
Bwhaaaah

Change to 2.5mm!!

CaptainBobSim, 2023-06-07:
Now it's #311

Closed 2023-06-07.

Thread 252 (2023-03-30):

whoops errors

CaptainBobSim, 2023-03-30:
But unfortunately I found errors:
in the Section 2 - Component Library and Structure/2-5 Instruments
in the folders Small_9_Servo/STLs,
the file - Servo Motor Plate.stl
is the same in content as the file - Servo SG90 Horn.stl
and the volume is the same 20kbytes.

CaptainBobSim, 2023-04-01:
Fixed!

Closed 2023-04-01.

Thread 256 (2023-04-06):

HDG PCB need Improvement

CaptainBobSim, 2023-04-06:

CaptainBobSim, 2023-05-16:
New and improved! Updated user experience, filleted stuff and improved the encoder footprint!

Closed 2023-05-16.

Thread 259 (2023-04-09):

Print these and add to project

CaptainBobSim, 2023-04-09:
[Small Dual Rotary Encoder for EC11 15mm (G1000 and other Panels) by Felte](https://www.thingiverse.com/thing:5160448)

CaptainBobSim, 2023-04-25:
Eh I'm pretty lazy and these have still a somewhat large footprint compared to dual concentric rotary encoders

Closed 2023-04-25.

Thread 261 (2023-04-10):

Annunciation is switch flipped?

CaptainBobSim, 2023-04-10:

CaptainBobSim, 2023-04-26:
Switched!

Closed 2023-04-26.

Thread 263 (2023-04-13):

Fix x27 footprint

CaptainBobSim, 2023-04-13:
I think I have it mirrored

CaptainBobSim, 2023-05-16:
Fixed and beautified!

Closed 2023-05-16.

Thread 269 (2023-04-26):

Altimeter gears should have higher module

CaptainBobSim, 2023-04-26:
Make it easier to "grab", ie higher allowance.

CaptainBobSim, 2023-05-16:
I haven't had any issue with this, but would be willing to change the design for V2 if needed

Closed 2023-05-16.

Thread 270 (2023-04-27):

Attitude Indicator cutout should have slot also turn coord

CaptainBobSim, 2023-04-27:

callahanp, 2023-04-28:
This is a photo of an instrument Shock Panel from a C172.  The part number is not identified on the part, so it may or may not be Cessna 172 Removable Instrument Shock Panel Assembly, P/N: 0513554-1  Which was current on the C172P in 1983, or it may be from an earlier or later model.

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

CaptainBobSim, 2023-04-28:
Nice!
The ruler comes in handy.

CaptainBobSim, 2023-06-07:
Finished!

Closed 2023-06-07.

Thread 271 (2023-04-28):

Make GNS530/GNS430 Open Source

CaptainBobSim, 2023-04-28:
- [ ] Setup a GitHub for the GNS 530/ 430
- [ ] Open Source it.
- [x] Make mounting system open source as a "Home Cockpit Standard" HCS - [ ] Make an open-source hall effect sensor module?
- [x] Make a GitHub for the Home Cockpit Standards

CaptainBobSim, 2023-06-26:
Not a priority - Flight Sim Maker is making one that's payware but not too bad

Closed 2023-06-26.

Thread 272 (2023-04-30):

USB extension instead of USB charger?

CaptainBobSim, 2023-04-30:
https://www.amazon.com/dp/B01NCA9XEI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

CaptainBobSim, 2023-06-07:
Put into BOM

Closed 2023-06-07.

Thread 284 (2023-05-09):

Revamp DFM Switch Panel PCB to maybe take care of pedestal functions??

CaptainBobSim, 2023-05-09:
Trim Pot
Trim 1234 motor
Pull Switch Cutoff
3/5 position selector (back L off R back vs L off R)

CaptainBobSim, 2023-05-09:
Merged!

Closed 2023-05-09.

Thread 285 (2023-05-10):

Simplify Startup sequence

CaptainBobSim, 2023-05-10:
- [ ] Organize Cables and make more obvious
- [ ] Create Shortcut
- [ ] Ready to Fly Skip
- [ ] Merge in Switch Panel
- [ ] Fix Turn Coordinator
- [ ] Fix Airspeed Indicator

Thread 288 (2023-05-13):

switch panel circuit board needs a bigger cutout

CaptainBobSim, 2023-05-13:
Fix this both on CAD and real life

and decrease size of board?

CaptainBobSim, 2023-06-26:
duplicate of #315

Closed 2023-06-26.

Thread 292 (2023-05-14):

Update JST Footprint :)

CaptainBobSim, 2023-05-14:

CaptainBobSim, 2023-05-17:
Hey that's awesome they were already fixed! Use JST XH Connectors v1-0 library :)

Closed 2023-05-17.

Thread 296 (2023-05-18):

Correct the pedestal height!!

CaptainBobSim, 2023-05-18:
Shorten it to account for carpet then include little adjust screws to raise height?
Drill screws as pilot holes only half way through

CaptainBobSim, 2023-12-09:
This is parametrized in the model.

Closed 2023-12-09.

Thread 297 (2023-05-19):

Stop printing logo in margins

CaptainBobSim, 2023-05-19:
It makes a mess

CaptainBobSim, 2023-12-09:
This should be all fixed, let me know if it isn't!

Closed 2023-12-09.

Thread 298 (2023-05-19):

maybe have the pedestal have finger joints

CaptainBobSim, 2023-05-19:

CaptainBobSim, 2023-06-28:
This will decrease the look of this so I don't want to make this a version - Let me know if you think differently!

Closed 2023-06-28.

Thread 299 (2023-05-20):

Fix annunciator flashing issue

CaptainBobSim, 2023-05-20:

CaptainBobSim, 2023-12-09:
Arduino has stopped flashing. With new beta update I will implement flashing for warnings (eventually)

Closed 2023-12-09.

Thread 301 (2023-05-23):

I might tweak airplaneee so that direction doesn't matter, and will upload the STL to GitHub.

CaptainBobSim, 2023-05-23:

CaptainBobSim, 2023-05-23:
Now there is "Back" Text to avoid confusion

Closed 2023-05-23.

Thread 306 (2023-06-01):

Stepper Gear Differences

feldon30, 2023-06-01:
10K Stepper Gear.stl and 1K Stepper Gear.stl have a different slot size for the 28BYJ-48 steppers.

CaptainBobSim, 2023-06-02:
They are now matching, and have the T-Shirts to prove it :)

Closed 2023-06-02.

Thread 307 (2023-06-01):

Altimeter Wheel Gear Retainer

feldon30, 2023-06-01:
A possibly modification to the Altimeter assembly would be to add two indentations to the Faceplate on the center column and then create a retaining ring that's 27mm OD, 11mm ID, 2mm thick with 2 pegs that would be pushed into (or glued) to the faceplate. The Wheel Gear would be able to spin freely but would be held captive to the faceplate.

CaptainBobSim, 2023-06-06:
I put in a retainer attached to the 10K gear, we'll see how this works.
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

I didn't want to glue it because I'm trying to avoid glue in this project to be maintenance friendly.
I couldn't screw the retainer in without using M2 screws which are also being avoided because they are generally annoying to work with.

CaptainBobSim, 2023-06-07:
Tested and works well!
Does not interfere with card gear.

feldon30, 2023-06-07:
Awesome!

CaptainBobSim, 2023-06-07:
Yep!

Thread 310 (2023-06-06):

x27 m2 hole size footprint needs to be bigger

CaptainBobSim, 2023-06-06:

CaptainBobSim, 2024-02-01:
Fixed!

Closed 2024-02-01.

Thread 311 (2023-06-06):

Adapt C172 Project for M2 Inserts for instruments

CaptainBobSim, 2023-06-06:
Switching back to M2 as M2 is the standard lowest screw in most packs of screw assortments
Holes will be sized above M2 as to self tighten to an M2.5 screw but use heat set inserts for M2 screws

1.9 and 2mm respectively

Closed 2023-12-09.

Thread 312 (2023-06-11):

Circuit Breaker Concerns

CaptainBobSim, 2023-06-11:
There's a lot here, reply with "unable" if you don't have time to read through this or reply in detail at the moment.

1.   My simulation program will trip the breaker if you click on it with the mouse.  This is useful in simulating an electrical problem.  Also, the property representing the state of the breaker is accessible and settable from outside the program.

 In the real C172 cockpit, can one can press on a circuit breaker to turn the circuit off?  I'm not sure.  The sample circuit breaker I bought on e-bay does not disconnect on press, but latches if you press on the tripped breaker.   I don't think you can use the real breakers as a switch.  I'm not sure about the avionics switch, but I suspect it might also act as a breaker.

2. I took a look at your Circuit breaker video.   I'm thinking about how the simulated circuit breakers in the cockpit interact with the simulation program. My simulation program can trigger the circuit breakers to trip in a simulation scenario by setting a property, but we want user interaction in the cockpit to mimic real world actions, driving the simulation program with the physical state of the simulated breakers from the cockpit.

3. Unfortunately, the solenoid you purchased from Ali-express, is no longer available from the link you gave in the video.  That's the problem with Ali-express.  I suspect that some the vendors there are selling  stuff that is dumped by manufacturers as obsolete, out of spec, or overstock, and is generally not a reliable supplier for components that you want to be available over the long term.  Pay attention to the "xxx available note"

There is an alternative that might provide the "pop" and has a latching mechanism in the in position, just like a circuit breaker.  And they're only 50 cents each!
The actuation current on these is approximately 675 ma and although they're rated at 5V, I was able to get them to trigger with 675ma at 1.7 volts up through about 3 volts. I was unable to measure the current above that voltage because I couldn't get the current limiting feature of my power supply to work beyond 3 v.  (operator problem maybe...) But given how these things work, the current is probably still 675 ma

4.
With the breaker in the physical cockpit, I'd want to be able to trigger the breaker by pressing on the physical breaker, causing the property in the simulation program to change to "off". At that point, the simulation program state has changed, and I'd like the breaker in the cockpit to pop out.  Similarly, if the popped out breaker is pressed back in, I'd like it to stay in, but also tell the simulation program that the breaker is reset and the circuit is no "on".

For silent operation, I'd use a transistor to give them a pulse of current. No relay clacking for the pulse, and fairly cheap too.  We'll see. Maybe your solution is better or cheaper.

 The mounting would be a re-design, and I'd want to add a micro switch or hall effect sensor to signal the simulation program the state of the physical circuit breaker.  These things are a bit wide at 13 mm, and an actual breaker is 14.2 mm across. Also, these pop with quite a bit of force, and I'm concerned about the longevity of a 3d printed mounting for them.  PLA layers don't take too much force to separate, and under repeated pounding and the 3 lb 10 oz force needed to reset the solenoid they might not hold up.  I'd be concerned about the 3d printed panel holding the breakers as well. (What do you think?

Also, there's no mounting holes, so maybe drill and tap, or just enclose in plastic  My guess is I'll end up making some kind of metal frame, drill and tap the solenoid frame for mounting and add some force dampening arrangement to connect them to the breaker's shaft while still providing the ability to reset it by pressing the tripped breaker. Mechanical design.  So much harder than software.

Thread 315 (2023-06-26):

Analog Backing Panel Revamp

CaptainBobSim, 2023-06-26:
- [x] Switch panel circuit board needs a bigger cutout #288
- [x] Use new push pull cutout of 38x24mm
- [x] Screw holes for dual pots
- [x] Holes for radio stack mounting
- [x] Hole for ELT mounting
- [x] Heat and Cool buttons - ADD SUPPORT HOLES
- [x] Half the glairsheild lip
- [x] Glareshield mounting holes
- [x] EXPORT EXPORT EXPORT

CaptainBobSim, 2023-06-28:
We did it!!

Closed 2023-06-28.

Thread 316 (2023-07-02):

Upgrade Six Pack Instrument Graphics

feldon30, 2023-07-02:
Six Pack instrument graphics seem to be derived from different origins in different qualities.
Recreate/trace graphics into scaleable vector format.

CaptainBobSim, 2023-07-02:
Hello! All of the 6-pack instruments except the Airspeed are vectorized. Any quality issues are from export.
Would you want to trace/replicate the Airspeed Indicator in an editable SVG format?

Graphic design is done in Inscape (open source tool) to make collaboration not locked into a paid platform. If needed you can do it in Adobe Illustrator.

The template for Inkscape SVGs is in
The-Cessna-172-Project-V3\Section 0 - Info and Full Assembly\--- COMPONENT TEMPLATE\___Decals.svg

CaptainBobSim, 2024-10-05:
I believe most are "die cut" format now, feel free to speak up if I missed any.
Thank you again @feldon30 for making these AMAZING decals!

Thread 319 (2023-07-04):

Part Number Idea

CaptainBobSim, 2023-07-04:
A viewer commented:
If you gave out free plans, but gave each piece a "part number" that you could either 3-d print or order would be a good compromise. It would give those who have the equipment the ability to make the part, those who don't have the equipment would be able to just order the part, and those who just want it to be done already could just order the part. In regards to the pricing, I would just make sure that if you went and decided to order every part in the entire setup that it would fall under a certain price limit. I would imagine that limit being just under 4,000$

CaptainBobSim, 2024-02-11:
I am going to divide it into products based on components and manufacturing process:
Airspeed Indicator - Bezel and Glass
Airspeed Indicator - PCB
Airpseed Indicator - Kit/Assembled

also
All Bezels
All Glass

Closed 2024-02-11.

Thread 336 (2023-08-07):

Use Carbon Fiber tubes instead of depending on weird parts

CaptainBobSim, 2023-08-07:
Carbon Fiber tubing can be a strong solution to bonding parts together and aligning instead of whatever the heck I'm doing with the yoke.
3mm thickness is standard!!
This can be standardized and a 3D printed dowel option can be optional (weak but okay)
Make sure to use one standard diameter/thickness through the project!

CaptainBobSim, 2024-01-27:
This is a cool idea, but I'd likely use 3D printed joints to not deal with sourcing these dowels.

Closed 2024-01-27.

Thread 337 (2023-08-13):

Make 5V system out of 12V system

CaptainBobSim, 2023-08-13:
12V--> 5V
via voltage regulator if on PCB
via buck converter if in general
Need to figure out if I'm going to step down for each PCB or not.
Need to decide on 5V wiring standard (currently it's screw terminals as to not confuse DC jacks with 12V)

CaptainBobSim, 2024-01-27:
I've decided that 12V powers each arduino breakout board. If you need 5V input you can buck convert it down. A lot of the boards will give you the option to use 5V or 12V (internal regulator)

Closed 2024-01-27.

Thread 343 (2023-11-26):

Some holes are misssized

CaptainBobSim, 2023-11-26:
Some holes are too big they should all be the same kinda

CaptainBobSim, 2023-12-07:
Completed on the panel update #347

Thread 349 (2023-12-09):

PCB Errors

CaptainBobSim, 2023-12-09:
- [x] 6 pack:
- [x] "ATT POT" on 6 Pack
- [x] "31 Zero ATT" and 31 on ALT
- [x] "D7" instead of "D17" (Might be on switch panel ALT BATT)
- [x] Change to JST-XH Double Head

CaptainBobSim, 2023-12-22:
We got em

Closed 2023-12-22.

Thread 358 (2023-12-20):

This issue has issues

CaptainBobSim, 2023-12-20:
- [x] Annun create 100 ohm text
- [x] Move winterization text up on panel
- [x] The M2 Airspeed Nub hole needs to be tighter
- [x] Make an "Orange Batch" for production
- [ ] Lenses and Bezel issue - too tight!

[image](https://github.com/CaptainBobSim/The-Cessna-172-Project-V3/assets/76851401/81509e6a-cd3c-426d-87f5-a4625636d82f)

Also hole size on panel for instruments should be bigger
Also attitude inst panel should be slightly bigger and everything else should be a tad smaller

CaptainBobSim, 2024-01-27:
Complete!

Closed 2024-01-27.

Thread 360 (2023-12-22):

Ensure that Pin 1 goes to Pin 1 with extension cables (flipped vs not flipped)

CaptainBobSim, 2023-12-22:
a detent for female pin retention and the detent up (facing you), left is signal, center is positive, and right is ground.  Early on, Airtronics/SanwaSanyo and Volz were different.  Airtronics eventually switched to that standard, and Volz went mostly commercial UAV (it seems).  I do not have any of its current servos to examine.  The reason for having V+ in the center was to protect from destroying the servo if inserted with reverse polarity.

For 2-pin connectors, I have continued to follow that order:  When held with the retention barb or detent up, red/positive on the left and ground on the right.  Of course, that is arbitrary with respect to the crimp.  One could change their standard to orient to the crimp.   With barbs, that is often opposite the crimp; whereas, with "Berg-type" detent-retained female pins, it is usually the same side as the crimp.

Also make sure that JST is on 6 Pack PCB

CaptainBobSim, 2024-01-18:
This should be good!

Closed 2024-01-18.

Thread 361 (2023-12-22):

6 Pack PCB

CaptainBobSim, 2023-12-22:
for 6 Pack - have options for steppers via JST or using the 4 in pins per motor.
JST is standard :)
Should I use the diodes?

Closed 2023-12-22.

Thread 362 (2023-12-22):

Mark 2 Switch Panel

CaptainBobSim, 2023-12-22:
- [ ] CB- Put in cable relief
- [x] Label ALL pins :{
- [x] 4 signal wires to stepper trim on dfm switch
- [x] 3rd toggle switch position might be off of center
- [ ] swap AV1 and AV2 so that plugging in is logical (also for batt/alt)
- [ ] CLEAR PATH FOR ARD USB CONNECTOR!!!
- [x] Must have either 2 acrylic panels OR Metal
- [x] Uses small circuit board toggles with large handle?
- [x] Little Mega soldered to board
- [x] Allows space for Circuit Breakers
- [x] Area for circuit board:
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
- [ ] Easier Key
- [x] Backlighting?
- [ ] XP and FS2020 compatible files
- [x] If we shift up Mark2 SW Panel we also need to shift Mark1 CB Panel up the same amount #289 No we don't these are different Z axis just make sure don't affect CB size

Switch Panel Improvements
fix F360 parametric height
CB Decals
Key Bill of Materials
Switch Drawing update ugly

Trim Pot
Trim 1234 motor
Pull Switch Cutoff
3/5 position selector (back L off R back vs L off R)

Make sure IDC connectors have enough room

Closed 2023-12-31.

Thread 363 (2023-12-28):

KMA 28 Audio Panel

CaptainBobSim, 2023-12-28:
Design Issues:
- [ ] Photosensor
- [ ] Figure out the screws
- [ ] Making a pillar support for the button skirt/mounting part. Maybe make it a M3 spacer friendly number for PCB
- [ ] Make PCB lighting??????????????????? Or use led strips
- [ ] Decals
- [x] P:ut in resistors
- [ ] Make LEDs mutually exclusive with LED Switches???????
- [ ] Make
- [ ] Implement Backlighting
- [ ] Add Alignment nubs to parts that have decals
- [ ] Use line in to play aux. https://www.youtube.com/watch?v=Lt1iVFnWFxI

Prototype Issues:
- [ ]

Decals:
- [ ] Decals Printer Friendly Version
- [ ] Laser Engraving Friendly Version

PCB Checklist
- [ ] Ground Plane on bottom
- [ ] "Stay Spicy ✈" airplane :)
- [ ] Autoroute Traces
- [ ] Write Version Number on PCB
- [ ] CaptainBobSim.com
- [ ] Write all component names and Pins

Publishing Tasks:
- [ ] Add Wiring diagram PNG (Also add to video)
- [ ] Partslist on ReadMe (Also add to video)
- [ ] Rotate and export all STLs using Prusa for easy printability (no slicer rotate)
- [ ] Mounting Template .DXF and maybe PDF
- [ ] Attach .STEP and .f3d
- [ ] MobiFlight .mfmc file
- [ ] FS2020 Mobi .mcc
- [ ] X-Plane Mobi .mcc
- [ ] Take pictures
- [ ] Printables
The Printables version will not be updated. The best place to get it is here: https://captainbobsim.com/product/the-cessna-172-project-files/?customize_changeset_uuid=
Find the MobiFlight code under Section 2/Instrument
- [ ] Tweak the ReadMe
	- [ ] Video Here
	- [ ] Buy it as a Kit/Assembled
	- [ ] Download only this folder via: https://download-directory.github.io/
	- [ ] Pinout?
- [ ] Follow steps on product central https://www.notion.so/captainbobsim/Product-Central-fe05d96d32074a269806f0e77462978f
- [ ] Thumbnail for Video
- [ ] Add links to video

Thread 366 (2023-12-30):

Control OAT with PANEL LT

CaptainBobSim, 2023-12-30:
OAT display should be dimmed with PANEL LT dimmer

CaptainBobSim, 2024-01-27:
This can be done with a relay, but depends on your LCD module. I will put this in the OAT issue.

Closed 2024-01-27.

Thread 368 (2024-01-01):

Davtron Clock/OAT

CaptainBobSim, 2024-01-01:
Decals:
- [x] Decals Printer Friendly Version
- [ ] Laser Engraving Friendly Version

Prototype Issues:
- [x] LCD Spacers 1m More
- [x] Text on Bezel?
- [x] Change M3 to M2
- [x] 01:01 displays as 1:1
- [x] Make the buttons ~1mm bigger diameter?

Publishing Tasks:
- [x] Add Wiring diagram PNG (Also add to video)
- [x] Partslist on ReadMe (Also add to video)
- [x] Rotate and export all STLs using Prusa for easy printability (no slicer rotate)
- [x] Mounting Template .DXF and maybe PDF
- [x] Attach .STEP and .f3d
- [x] MobiFlight .mfmc file
- [x] FS2020 Mobi .mcc
- [ ] X-Plane Mobi .mcc
- [ ] Take pictures
- [x] Printables
The Printables version will not be updated. The best place to get it is here: https://captainbobsim.com/product/the-cessna-172-project-files/?customize_changeset_uuid=
Find the MobiFlight code under Section 2/Instrument
- [x] Tweak the ReadMe
	- [x] Video Here
	- [ ] Buy it as a Kit/Assembled
	- [ ] Download only this folder via: https://download-directory.github.io/
	- [x] Pinout?
- [ ] Follow steps on product central https://www.notion.so/captainbobsim/Product-Central-fe05d96d32074a269806f0e77462978f
- [x] Thumbnail for Video
- [x] Add links to video

Still Need to (Known issues, shelved for now - feel free to try and fix them!)
- [ ] Setting Universal Time
- [ ] Setting Local Time
- [ ] Setting Flight Time Alarm (With Sound)
- [x] Elapsed Time Count Up
- [ ] Elapsed Time Count down
- [ ] Correct formatting of voltage

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

CaptainBobSim, 2024-01-02:
Published, will add X-Plane later!

Closed 2024-01-02.

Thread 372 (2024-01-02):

U shape hole on CDI

CaptainBobSim, 2024-01-02:

CaptainBobSim, 2024-01-27:
Added to project issue

Closed 2024-01-27.

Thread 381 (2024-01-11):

KAP 140 widen holes for tabs on back of LCD

CaptainBobSim, 2024-01-11:
- [x] and move LCD headers and measure to be sure.

CaptainBobSim, 2024-01-27:
They can be easily bent, as of now it's not worth the circuit board redesign.
Bending the tabs can also create a somewhat "press fit" and snap the board into place.

Closed 2024-01-27.

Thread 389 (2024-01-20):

Put in PWM Dimming on 6 Pack PCB

CaptainBobSim, 2024-01-20:
Put in 6 LED Outputs
MOSFET
Resistors

Rename U1 to "Arduino Mega"
Redo Footprint for ULN Drivers

Rename ATT POT to ALT POT

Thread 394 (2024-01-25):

Overcome adversity in the console

CaptainBobSim, 2024-01-25:
Conflict
![Uploading 299505064...]

Image didn't uploading....
The Dimmers interfere with the pedestal, the pedestal lip should be cut down ~3-4mm

CaptainBobSim, 2024-01-27:
Yaaaaaay I loooooooovvvvvveeee reexporting tens of files and waiting for fusion 360 to crash while updating dependencies.

Closed 2024-01-27.

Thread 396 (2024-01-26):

Add Resistor Values and changelog to PCBs (all prototypes)

CaptainBobSim, 2024-01-26:
- [x] annun warn
- [x] GPS annun
- [x] KT 76
- [x] KMA 28
- [x] KAP 140
- [x] KN62A

CaptainBobSim, 2024-01-27:
Look at me! so consistent!

Closed 2024-01-27.

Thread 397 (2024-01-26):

Annun PCB Redo pin labels (too squishy)

CaptainBobSim, 2024-01-26:

CaptainBobSim, 2024-01-27:
The-Cessna-172-Project-V3\Section 2 - Component Library and Structure\2-6 Avionics, Radios, Annunciators\ANNUNCIATOR_Analog Warning\V5.0 Pinout.png

Desquished! 5.0 Pinout for reference

Closed 2024-01-27.

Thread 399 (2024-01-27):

Lenses and Bezel issue - too tight!

CaptainBobSim, 2024-01-27:

CaptainBobSim, 2024-02-09:
Inc from 0.15 to 0.35 mm clearance - different machines making each part warrants more than usual clearance.

Closed 2024-02-09.

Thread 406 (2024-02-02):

7 SEG Pinout is SOOOO WRONG

CaptainBobSim, 2024-02-02:
Apparently just clicking "Connect" a bunch of times is not a vaild strategy.

- [x] Rename 1-12 to actual pins
- [x] connect actual pins (footprint) to symbol pins

CaptainBobSim, 2024-02-07:
Done for 3 Digit, will check when I make other ones!

Closed 2024-02-07.

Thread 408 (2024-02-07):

KAP 140 right side (from front view) could remove some material on PCB to make space for PCB to sit flat

CaptainBobSim, 2024-02-07:

CaptainBobSim, 2024-02-10:
The LCD should sit flatter than the biscuits I made yesterday that looked more like burnt pancakes than anything meaningful.
Why was the gravy orange 😭😭😭😭😭😭

Closed 2024-02-10.

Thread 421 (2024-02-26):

redesign V2 PCB Switch panel to

CaptainBobSim, 2024-02-26:
A) Not warp panel
B) Not interfere with switches

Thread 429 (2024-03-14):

Design Glass for DME

CaptainBobSim, 2024-03-14:
Laser on back, words inverted, tinted and masked

CaptainBobSim, 2024-06-06:
D.U.N. Done!

Closed 2024-06-06.

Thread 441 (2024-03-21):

Progress Checklist

CaptainBobSim, 2024-03-21:
Cessna 172S Normal Operation Checklist

Based on [West House Airport’s](https://www.google.com/url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)

BEFORE STARTING ENGINE
- [ ] Preflight Inspection COMPLETE
- [ ] Passenger Briefing COMPLETE
- [ ] Seats & Seat Belts ADJUST & LOCK (ASSURE INERTIAL REEL LOCKING)
- [ ] Brakes TEST & SET
- [ ] Circuit Breakers CHECK ENGAGED (IN)
- [ ] Electrical Equipment OFF

WARNING
Avionics Power must be "OFF" during Engine Start to prevent damage to Avionics.

- [ ] Avionics Power Switch OFF
- [ ] Fuel Selector Valve BOTH
- [ ] Fuel Shut-Off Valve ON (PUSH FULL IN)

STARTING ENGINE -- Normal With Battery
- [ ] Throttle OPEN 1/4 INCH
- [ ] Mixture IDLE CUT-OFF
- [ ] Propeller & Blast Areas CLEAR VISUAL & (VERBAL WARNING)
- [ ] External Power (If Used) CONNECT
- [ ] Master Switch ON
- [ ] Flashing Beacon ON

NOTE
IF ENGINE IS WARM, OMIT PRIMING PROCEDURE of Step 7 & 8

- [ ] Aux. Fuel Pump Switch ON
- [ ] Mixture ADVANCE TO OBTAIN 3 to 5 GHP FUEL FLOW, THEN QUICKLY RETURN TO IDLE CUT-OFF POSITION
- [ ] Aux. Fuel Pump OFF
- [ ] Ignition Switch START (RELEASE WHEN ENGINE STARTS)
- [ ] Mixture ADVANCE SMOOTHLY to RICH WHEN ENGINE FIRES
- [ ] Throttle 1100 to 1200 RPM
- [ ] Oil Pressure CHECK (Must Start UP within 30 Seconds)
- [ ] Ammeter CHECK

WARNING
Ammeter should indicate some charge immediately after engine starts.

BEFORE TAXI
- [ ] Flashing Beacon ON
- [ ] Nav Lights (If Dark or Near Sunset) ON
- [ ] Avionics Power Switch ON
- [ ] Radios ON, SET FREQUENCIES, ADJUST VOLUME
- [ ] Transponder STANDBY
- [ ] Wing Flaps UP
- [ ] TAXIING
- [ ] Brakes TEST Before Taxiing More Than The Length of The Fuselage.
- [ ] Throttle USE MINIMUM POWER, Adjust As Needed. Use Brakes Only to SUPPLEMENT Power Adjustments.
- [ ] BEFORE TAKEOFF

Parking Brake SET
- [ ] Throttle 1100 to 1200 RPM
- [ ] Seat Backs UPRIGHT POSITION
- [ ] Seats & Seat Belts CHECK SECURE
- [ ] Cabin Doors CLOSED & LOCKED
- [ ] Flight Controls MOVE FREE IN PROPER DIRECTION
- [ ] Flight Instruments CHECK & SET
- [ ] Fuel Quantity CHECK
- [ ] Mixture RICH
- [ ] Fuel Selector Valve BOTH
- [ ] Elevator Trim SET FOR TAKEOFF
- [ ] BEFORE TAKEOFF (CONTINUATION)

- [ ]
- [ ] Throttle 1,800 RPM
- [ ] Magnetos CHECK
- [ ] [RPM Drop should not exceed 150 RPM on a single magneto, or 50 RPM difference between the magnetos.]
- [ ] Vacuum Gauge CHECK
- [ ] Engine Instruments & Ammeter CHECK
- [ ] Throttle 1100 to 1200 RPM
- [ ] Throttle Friction Lock ADJUST
- [ ] Taxi Light ON
- [ ] Strobe Light ON
- [ ] Radios & AvionicsS SET FREQUENCIES & VOLUME
- [ ] Transponder SET ALTITUDE & CORRECT CODE
- [ ] Auto-Pilot OFF
- [ ] Wing Flaps SET FOR TAKEOFF
- [ ] Brakes RELEASE
- [ ] THE SCHOOL RECOMMENDS using a TAXI LIGHT or LANDING LIGHT when operating in or within one mile of the Airport Traffic Pattern to aid others in seeing you.

TAKEOFF - Normal
- [ ] Flaps 0° to 10°
- [ ] Throttle 3. Mixture FULL OPEN RICH (Above 3,000 MSL, LEAN to MAXIMUM RPM
- [ ] Elevator Control LIFT NOSE (ROTATE) at 55 Kts 70 to 80 Kts (Recommend VY 74 Kts) 5. Climb Airspeed
- [ ] TAKEOFF - Short Field
- [ ] Flaps 10°
- [ ] Brakes APPLY
- [ ] Throttle FULL OPEN (Smoothly)
- [ ] Mixture RICH (Above 3,000 MSL, LEAN to MAXIMUM RPM)
- [ ] Brakes RELEASE
- [ ] Elevator Control SLIGHTLY NOSE HIGH
- [ ] Flaps 7. Climb Airspeed UP After Reaching 60 Kts. 56 Kts UNTIL ALL OBSTACLES CLEARED

ENROUTE CLIMB
- [ ] Landing & Taxi Lights OFF
- [ ] Throttle FULL OPEN
- [ ] Mixture RICH (Above 3,000 MSL, LEAN to MAX. RPM)
- [ ] If maximum performance climb is necessary, consult Pilots Operating Handbook, Section 5, RATE-OF-CLIMB Chart.
- [ ] Airspeed 70 to 85 Kts (Recommend Vý 74 Kts)

CRUISE
- [ ] Power ....... 65% (Usually obtained by 2,300 to 2,400 RPM) ADJUST
- [ ] Elevator Trim
- [ ] Mixture LEAN to BEST POWER SETTING (Excessive Leaning May Damage Engine Severely.)
- [ ] DESCENT
- [ ] Fuel Selector Valve BOTH
- [ ] Power AS DESIRED

[WARNING] Reducing power below 1500 RPM without reducing airspeed may cause excessive engine cooling.

Mixture For Idle Power ADJUST for SMOOTH OPERATION FULL RICH

BEFORE LANDING (Mid Part of Down-Wind Leg)or Before)
- [ ] Taxi Light ON
- [ ] Seat Belts & Shoulder Harness SECURE
- [ ] Seat Backs MOST UPRIGHT POSITION
- [ ] Fuel Selector Valve BOTH
- [ ] Mixture RICH
- [ ] Auto-Pilot. OFF
- [ ] Radios (Frequencies, Volume) SET

LANDING -- Normal
- [ ] Airspeed 65 to 70 Kts
- [ ] Flaps AS DESIRED [0° to 10° below 110 Kts]
- [ ] Airspeed Minimum [10+ below 85 Kts] 0 62 Kts with Flaps 30
- [ ] Touchdown MAIN WHEELS FIRST
- [ ] Landing Roll ALLOW NOSE WHEEL to LOWER GENTLY
- [ ] Brakes MINIMUM REQUIRED [Aerodynamic Braking recommended to supplement wheel brakes]
- [ ] LANDING - Short Field
- [ ] Airspeed 65 Kts (With Flaps 0)
- [ ] Flaps EXTEND AS NEEDED UNTIL 30
- [ ] Airspeed On Final Approach 61 Kts [Until Flare-Out]
- [ ] Power REDUCE TO IDLE When Obstacles Cleared
- [ ] Touchdown MAIN WHEELS FIRST
- [ ] Brakes [When Firmly On Ground] APPLY HEAVILY
- [ ] Flaps *** DO NOT SKID TIRES *** RETRACT if having difficulty with traction

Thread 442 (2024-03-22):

Backlighting Tips for Avionics

CaptainBobSim, 2024-03-22:
For backlight control you should look into wiring a separate GND wire for the leds and having an n-channel FET control this GND connection.
Starting a thread for this to keep the main channel tidy
If you are designing a PCB and need to control a lot of LEDs you are better off adding a dedicated LED driver chip like the DM13A to your design and having that manage the LEDs for you. Mobiflight sees it as an output shift register.

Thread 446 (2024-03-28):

Pin 13 Strange behavior

CaptainBobSim, 2024-03-28:

oOblik, 2024-04-06:
This is a known thing https://docs.arduino.cc/learn/microcontrollers/digital-pins/

> Digital pin 13 is harder to use as a digital input than the other digital pins because it has an LED and resistor attached to it that's soldered to the board on most boards. If you enable its internal 20k pull-up resistor, it will hang at around 1.7V instead of the expected 5V because the onboard LED and series resistor pull the voltage level down, meaning it always returns LOW. If you must use pin 13 as a digital input, set its pinMode() to INPUT and use an external pull down resistor.

CaptainBobSim, 2024-06-06:
This has been fixed with the redesigned Breakout Board System (V2.0)

Closed 2024-06-06.

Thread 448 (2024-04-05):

Radio: Did you notice you have NAV labeled as COMM in your designs?

CaptainBobSim, 2024-04-05:

oOblik, 2024-04-05:
To add to this, as I put the radio together there are a few other minor things I found that you may or may not want to update (they are very nitpick-y I know):

Having a notch to accommodate the little pin that sticks out of the front of the dual-encoders that prevent them from rotating when used would be nice. Right now they press against the back of the front plate and kind of force them to sit crooked. It also makes it much harder to properly tighten them down.

On the PropWashSim Dual 5 Digit display, the header isn't completely behind the segment LEDs and the solder points on the other side of the PCB prevent it from sitting flush on the enclosure. Having a small (~1mm) indent in between the displays to accommodate the solder points would solve that.

CaptainBobSim, 2024-04-06:
Hey @oOblik Could you draw these out, I'm having a hard time understanding exactly what you're saying

CaptainBobSim, 2024-04-08:
Ahh, thanks for showing me! Usually those would be clipped with side snips but it would be a good design feature to put in a cavity (especially for the encoder - to stop bad rotation)

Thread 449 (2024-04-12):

Instrument panel troubles

CaptainBobSim, 2024-04-12:
I hope you well and doing great.

    So today I thought I would continue my IP build, I spent a few hours printing and putting together the plan for the stiffner/back board, I transfer everything with carbon paper.

     However when I've come to cut it out and start drilling the holes that this one isn't anywhere near close especially mounting holes and screw and bolt holes., and I searched your git hub for another file that related to my IP and didn't find anything ( which I find a confusing platform) well that and Discord.

 Can you shed any light on this at all please?

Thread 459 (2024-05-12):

Rework BOB Pin 13

CaptainBobSim, 2024-05-12:

CaptainBobSim, 2024-05-21:
reworked! It's now a PWM signal for use with MOSFET (or can be ignored - recommended)

Closed 2024-05-21.

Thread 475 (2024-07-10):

Reconnect these 👉👈

CaptainBobSim, 2024-07-10:
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

CaptainBobSim, 2024-07-19:
I have no clue what I'm looking at but I'm pretty sure I solved it.
Ohhh yep those traces are connected again.

Closed 2024-07-19.

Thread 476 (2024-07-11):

fix the fweaking panel file

CaptainBobSim, 2024-07-11:
it keeps getting fweaked up, which fweaks me up.

CaptainBobSim, 2024-08-02:
Inkscape issue appears to be an issue with selection when copying.

File reverted to prior version, updated save material panel exported then implemented.

Closed 2024-08-02.

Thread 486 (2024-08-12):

COM NAV GND Fault? Make sure COM Encoder works before GNS 530 PCB Release

CaptainBobSim, 2024-08-12:

ecdcrew, 2024-09-20:
Do you do "auto route" on easyEDA? Some times the distance between paths does run an electrical short (like 1 in every 30 PCBS)

CaptainBobSim, 2024-09-20:
I forgot I still had this opened! It was actually an issue that I didn't have it configured in Mobiflight 🤦‍♂️

Closed 2024-09-20.

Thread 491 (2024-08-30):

Tasks for showcase

CaptainBobSim, 2024-08-30:
Conterbore Throttle Holes
Alt Static Hole to 3.2 & longer
65cm push pull heat
45cm ALT STATIC
~60cm Flaps

print yoke
print adf mounts
grommet
solder and config trim

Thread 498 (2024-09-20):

Make Buttons for 530 kit without labels

ecdcrew, 2024-09-20:
For kit buyers, 80% (or more) will benefit from labels (OBS, VNAV, FPL etc) embossed on the button itself, as you have done. However, for those of us with Lasers (CNC) it would be cool to have no raised labels on buttons. Please consider this a VERY low priority item (but you can apply the logic to all buttons in all kits).

I print in white, spray paint black, then let the laser do the magic of removing the .3mm of black paint to reveal detailed text.

CaptainBobSim, 2024-09-20:
If you ever want to make an inkscape file with the labeling I'd be down to include this in the project files!
Regardless I'll put it in my someday list :)

ecdcrew, 2024-09-20:
Actually, I meant the STL button, not a label file. Literally, your tall and short buttons have text on them for the 530 kit, I'm saying leave them as plain buttons.

RE: [Button_tall.stl](https://github.com/CaptainBobSim/The-Cessna-172-Project-V3/blob/main/Section%202%20-%20Component%20Library%20and%20Structure/2-6%20Avionics%2C%20Radios%2C%20Annuncia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) etc.

CaptainBobSim, 2024-09-20:
For sure! I've just exported the STLs (I just performed a cut in Bambu Slicer), if you have an SVG file to send to a cutter I think that could be helpful for people? If that's something you want to make it could be super dope! but if not I can do it sometime :)

CaptainBobSim, 2024-09-20:
Only if you'd already do it or if you want to though!

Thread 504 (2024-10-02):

fuel panel PCB 5V != +5V

CaptainBobSim, 2024-10-02:

CaptainBobSim, 2024-10-05:
duplicate of #505
Not even like a cool twin or an evil twin, just a twin that takes too long of showers

Closed 2024-10-05.

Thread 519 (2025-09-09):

KR 87 ADF Radio Stack Thing

CaptainBobSim, 2025-09-09:
- [x] Mounting
- [x] Figure out 88:88 segment
- [x] Put in lighting via dimmer bus (Copy over XPNDR Circuitry)
- [x] definitely do better on the 10µF thingie!

Design Issues:
- [ ] Add Alignment nubs to parts that have decals
- [ ] Heat Set Inserts

Decals:
- [ ] Decals Printer Friendly Version
- [ ] Laser Engraving Friendly Version

PCB Checklist
- [x] Ground Plane on bottom
- [x] "Stay Spicy ✈" airplane :)
- [x] Autoroute Traces
- [x] Write Version Number on PCB
- [x] CaptainBobSim.com
- [x] Write all component names and Pins
- [x] Write resistor values: 150Ω red 100Ω white (at 5V!) 50Ω for sharing 4 white
- [x] Write Changelog - Top right, size 2.54mm
Changelog
V1.0 Initial Design (Date)

Prototype Issues:
- [ ]

Publishing Tasks:
- [ ] Add Wiring diagram PNG (Also add to video)
- [ ] Partslist on ReadMe (Also add to video)
- [ ] Rotate and export all STLs using Prusa for easy printability (no slicer rotate)
- [ ] Mounting Template .DXF and maybe PDF
- [ ] Attach .STEP and .f3d
- [ ] MobiFlight .mfmc file
- [ ] FS2020 Mobi .mcc
- [ ] X-Plane Mobi .mcc
- [ ] Take pictures
- [ ] Printables https://www.printables.com/model/create
The Printables version will not be updated. The best place to get it is here: https://captainbobsim.com/product/the-cessna-172-project-files/?customize_changeset_uuid=
Find the MobiFlight code under Section 2/Instrument
- [ ] Tweak the ReadMe
	- [ ] Video Here
	- [ ] Buy it as a Kit/Assembled
	- [ ] Download only this folder via: https://download-directory.github.io/
	- [ ] Pinout?
- [ ] Follow steps on product central https://www.notion.so/captainbobsim/Product-Central-fe05d96d32074a269806f0e77462978f
- [ ] Thumbnail for Video
- [ ] Add links to video

Closed 2025-09-09.

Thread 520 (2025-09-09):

KN-62A DME

CaptainBobSim, 2025-09-09:
- [x] Fix the slide switch footprint (give more space)
- [x] Move 7 Seg Displays down 0.5-1mm? Very thin 3d printed skirt?
Design Issues:
- [x] Add Alignment nubs to parts that have decals\
- [x] Make Laser Decal

Decals:
- [ ] Decals Printer Friendly Version
- [ ] Laser Engraving Friendly Version

PCB Checklist
- [x] Ground Plane on bottom
- [x] "Stay Spicy ✈" airplane :)
- [x] Autoroute Traces
- [x] Write Version Number on PCB
- [x] CaptainBobSim.com
- [x] Write all component names and Pins

Prototype Issues:
- [x]

Publishing Tasks:
- [ ] Add Wiring diagram PNG (Also add to video)
- [ ] Partslist on ReadMe (Also add to video)
- [ ] Rotate and export all STLs using Prusa for easy printability (no slicer rotate)
- [ ] Mounting Template .DXF and maybe PDF
- [ ] Attach .STEP and .f3d
- [ ] MobiFlight .mfmc file
- [ ] FS2020 Mobi .mcc
- [ ] X-Plane Mobi .mcc
- [ ] Take pictures
- [ ] Printables https://www.printables.com/model/create
The Printables version will not be updated. The best place to get it is here: https://captainbobsim.com/product/the-cessna-172-project-files/?customize_changeset_uuid=
Find the MobiFlight code under Section 2/Instrument
- [ ] Tweak the ReadMe
	- [ ] Video Here
	- [ ] Buy it as a Kit/Assembled
	- [ ] Download only this folder via: https://download-directory.github.io/
	- [ ] Pinout?
- [ ] Follow steps on product central https://www.notion.so/captainbobsim/Product-Central-fe05d96d32074a269806f0e77462978f
- [ ] Thumbnail for Video
- [ ] Add links to video

Closed 2025-09-09.

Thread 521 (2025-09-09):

Radio Stack Breakout

CaptainBobSim, 2025-09-09:
Design Issues
- [x] Replace Header with Correct Header
- [x] Prototype real "analog shorting"
- [x] Check the "analog shorting" to make sure it's correct
- [x] Double check traces
- [x] Double check status
- [x] Mirror text callouts to other side
- [x] Issue #385 Standard power supply
- [x] Add Alignment nubs to parts that have decals

Decals:
- [x] Decals Printer Friendly Version
- [x] Laser Engraving Friendly Version

PCB Checklist
- [x] Ground Plane on bottom
- [x] "Stay Spicy ✈" airplane :)
- [x] Autoroute Traces
- [x] Write Version Number on PCB
- [x] CaptainBobSim.com
- [x] Write all component names and Pins

Prototype Issues:
- [ ]

Publishing Tasks:
- [ ] Add Wiring diagram PNG (Also add to video)
- [ ] Partslist on ReadMe (Also add to video)
- [ ] Rotate and export all STLs using Prusa for easy printability (no slicer rotate)
- [ ] Mounting Template .DXF and maybe PDF
- [ ] Attach .STEP and .f3d
- [ ] MobiFlight .mfmc file
- [ ] FS2020 Mobi .mcc
- [ ] X-Plane Mobi .mcc
- [ ] Take pictures
- [ ] Printables https://www.printables.com/model/create
The Printables version will not be updated. The best place to get it is here: https://captainbobsim.com/product/the-cessna-172-project-files/?customize_changeset_uuid=
Find the MobiFlight code under Section 2/Instrument
- [ ] Tweak the ReadMe
	- [ ] Video Here
	- [ ] Buy it as a Kit/Assembled
	- [ ] Download only this folder via: https://download-directory.github.io/
	- [ ] Pinout?
- [ ] Follow steps on product central https://www.notion.so/captainbobsim/Product-Central-fe05d96d32074a269806f0e77462978f
- [ ] Thumbnail for Video
- [ ] Add links to video

Closed 2025-09-09.

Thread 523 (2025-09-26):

KT-76 Intermittent Display Error

CaptainBobSim, 2025-09-26:
Hi, having a slight issue with the KT-76 transponder.

it seems to work except the part where if you press a button less than 4 times, it doesn't show the intermittent display like '1---'...

I do have some time to debug this, so i was wondering if you send me the version i see in the video where it's working?...in my version of the mobi flight config, the 'xpndrcode display' variable is disabled, and if i enable, it shows an error in the logs. (Attached)

Fixed here:

https://github.com/shudecek/FlightSim-SimConnect-Python?tab=readme-ov-file

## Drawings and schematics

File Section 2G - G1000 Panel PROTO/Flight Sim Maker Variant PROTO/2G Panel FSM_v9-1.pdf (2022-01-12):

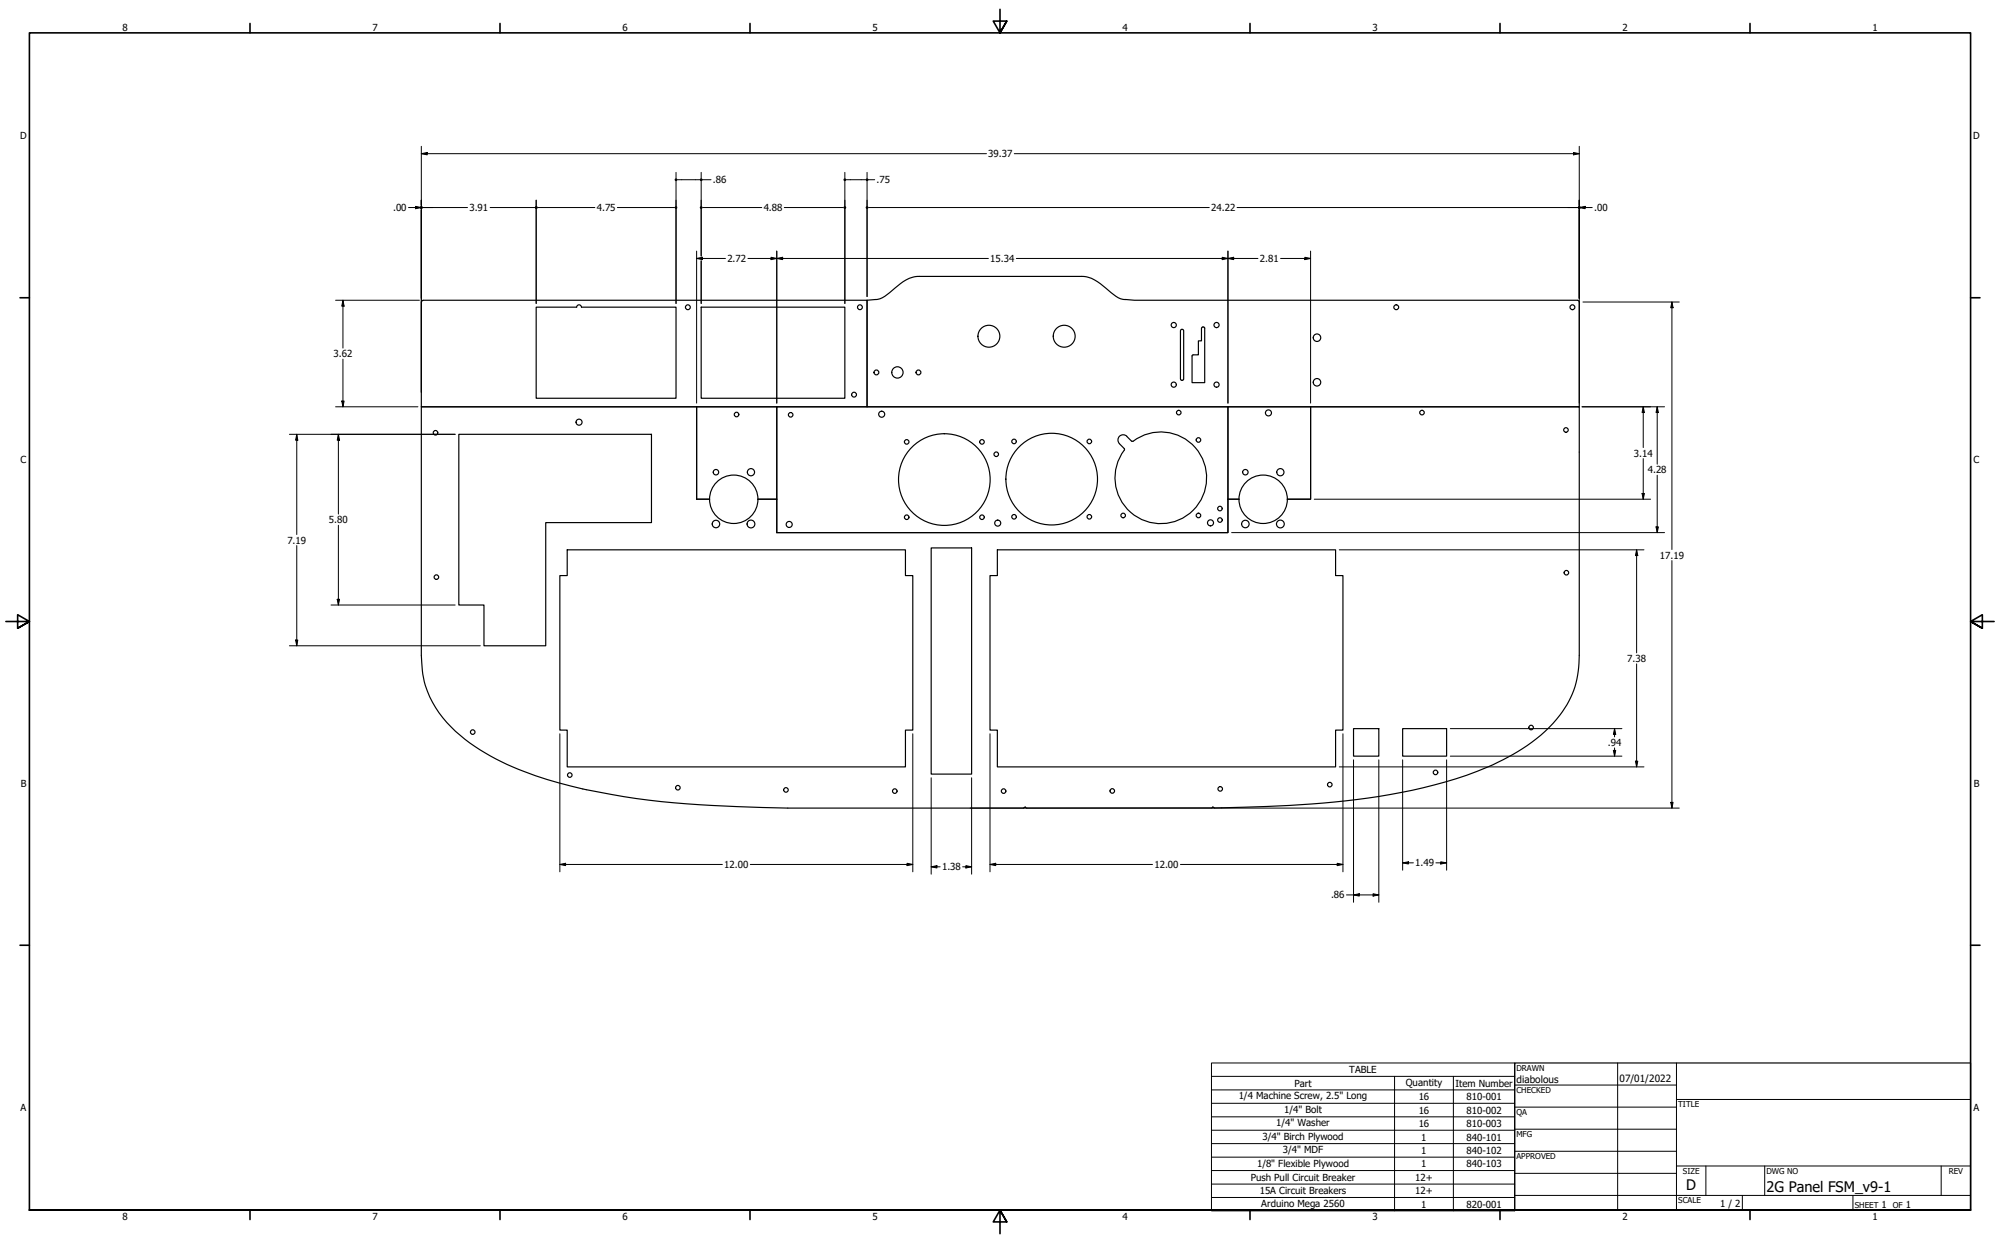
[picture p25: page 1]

TABLE | DRAWN diabolous | 07/01/2022

Part | Quantity | Item Number

CHECKED

1/4 Machine Screw, 2.5" Long | 16 | 810-001

1/4" Bolt | 16 | 810-002
1/4" Washer | 16 | 810-003
3/4" Birch Plywood | 1 | 840-101 | MFG
3/4" MDF | 1 | 840-102
1/8" Flexible Plywood | 1 | 840-103
Push Pull Circuit Breaker | 12+
15A Circuit Breakers | 12+
Arduino Mega 2560 | 1 | 820-001

APPROVED

SIZE D | DWG NO 2G Panel FSM_v9-1 | REV

SCALE 1 / 2 | | SHEET 1 OF 1

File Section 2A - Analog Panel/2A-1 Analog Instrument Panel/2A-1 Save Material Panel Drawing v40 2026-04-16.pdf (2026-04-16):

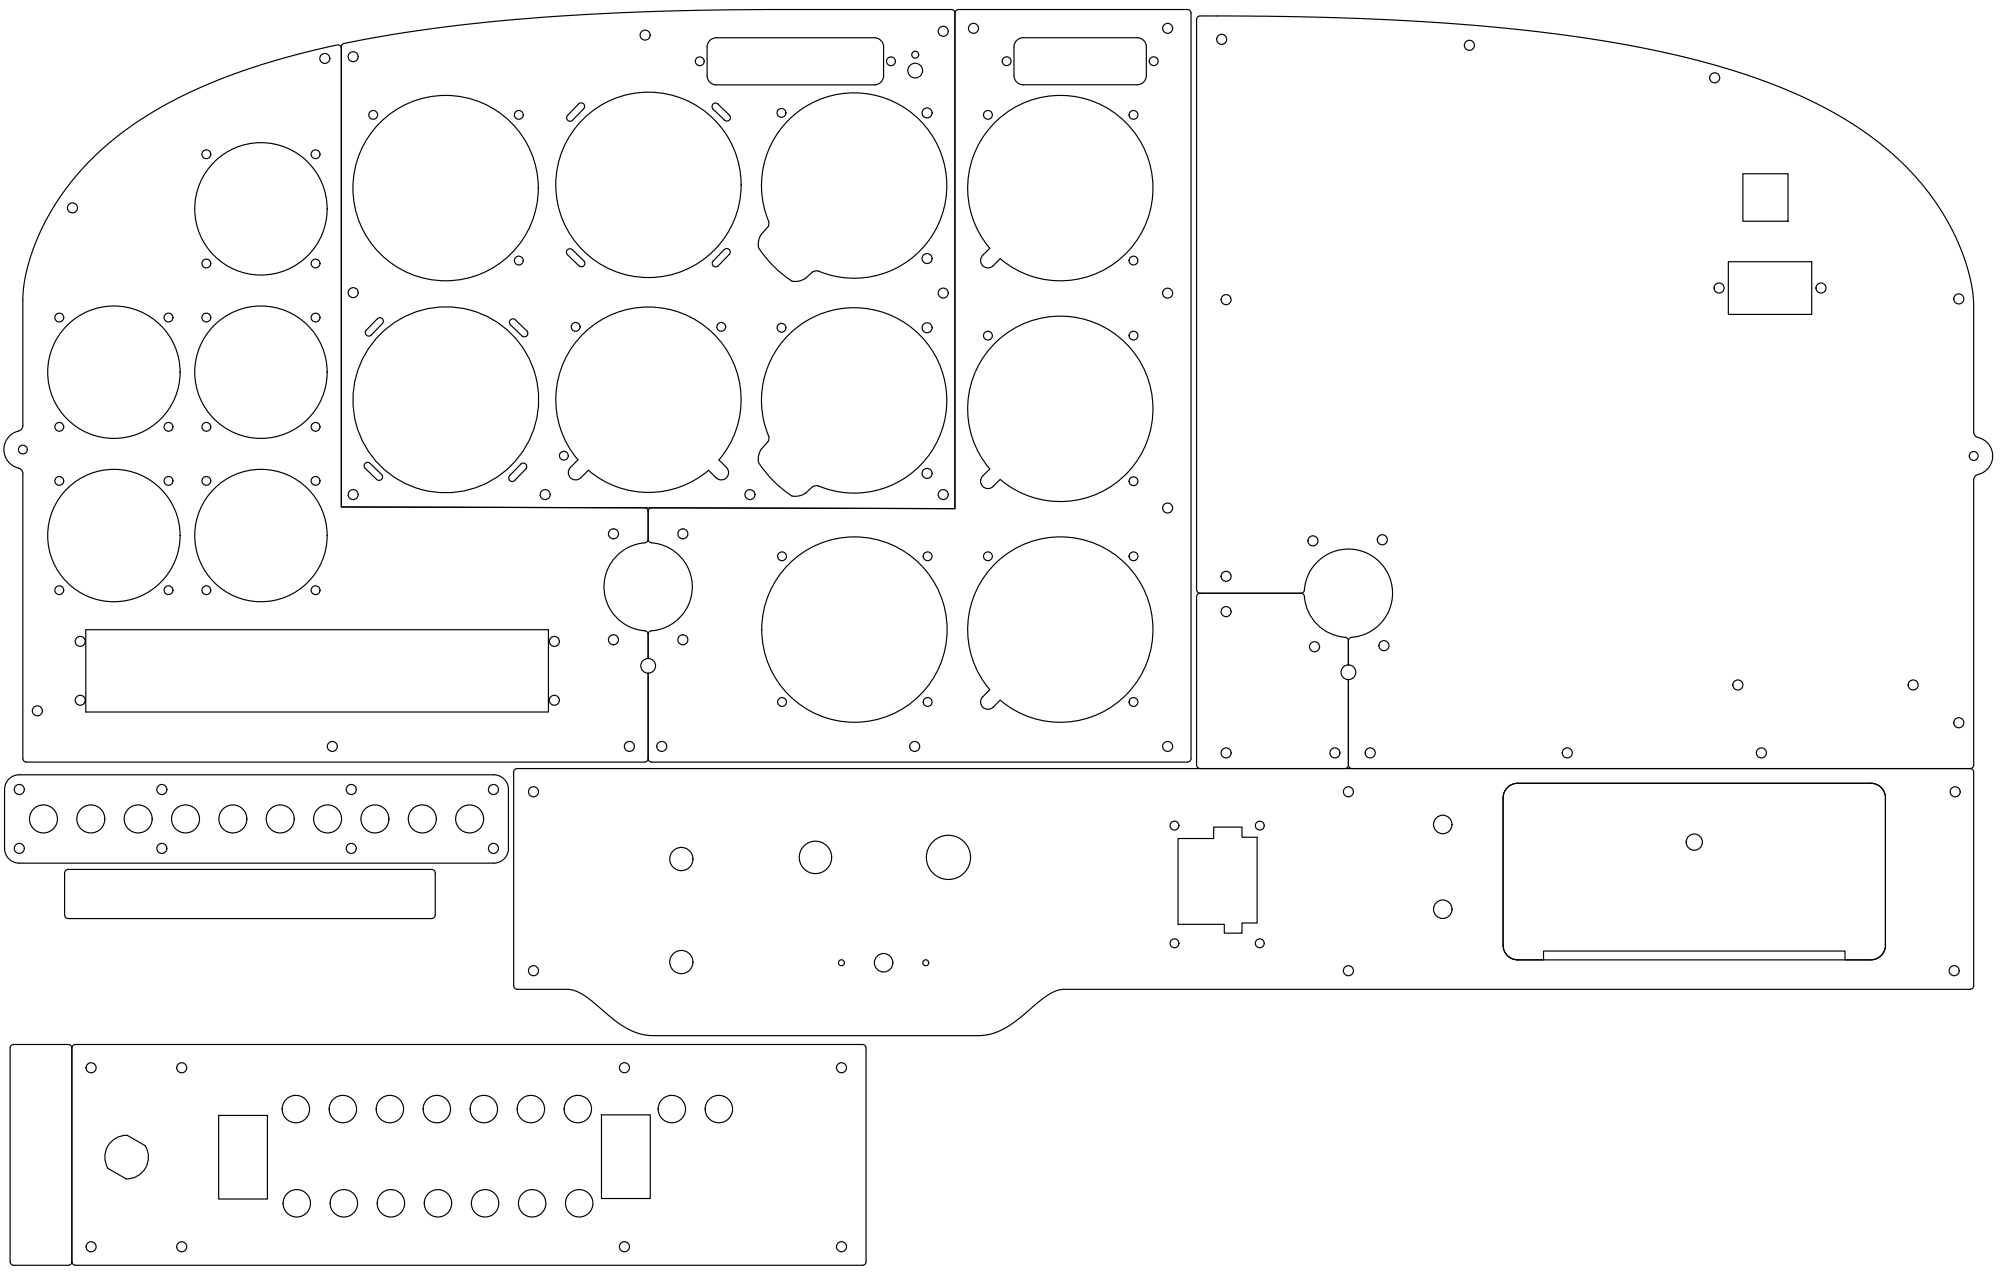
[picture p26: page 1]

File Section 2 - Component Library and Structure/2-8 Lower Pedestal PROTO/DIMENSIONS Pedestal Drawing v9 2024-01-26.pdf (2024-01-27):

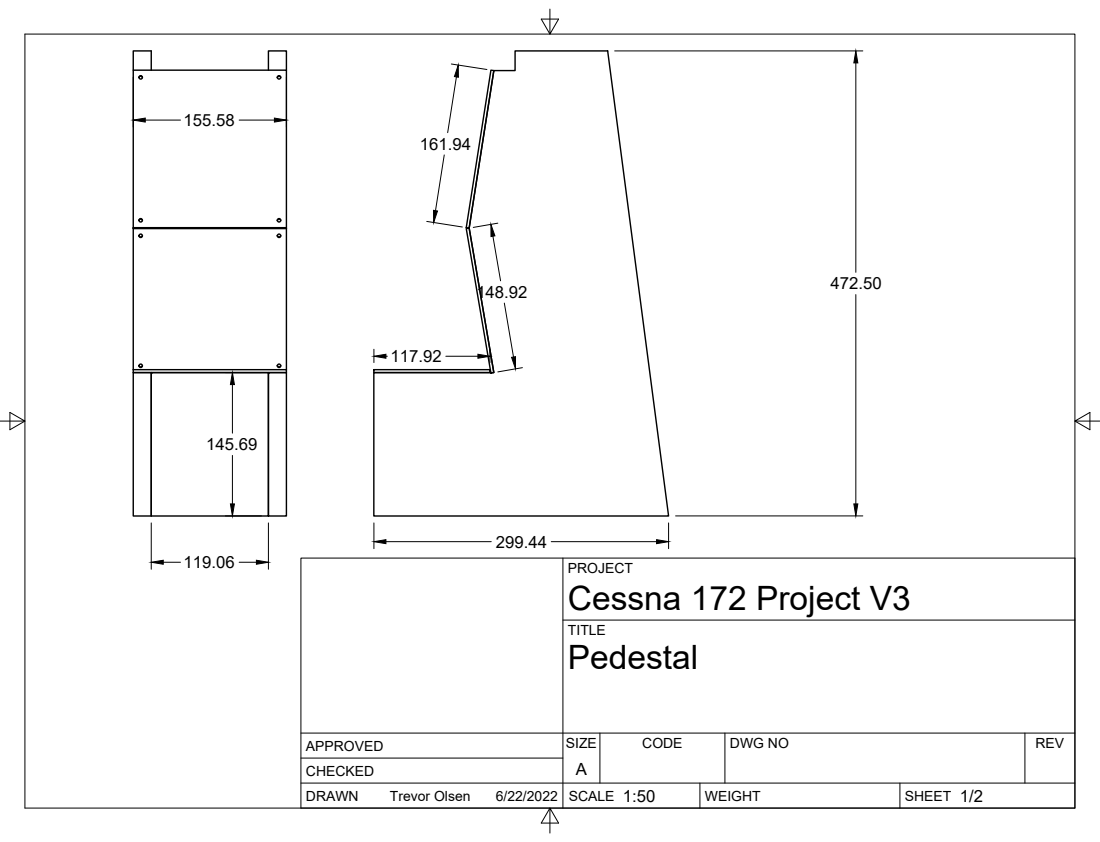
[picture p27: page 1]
SIZE; CODE; DWG NO; REV; Trevor Olsen; Cessna 172 Project V3

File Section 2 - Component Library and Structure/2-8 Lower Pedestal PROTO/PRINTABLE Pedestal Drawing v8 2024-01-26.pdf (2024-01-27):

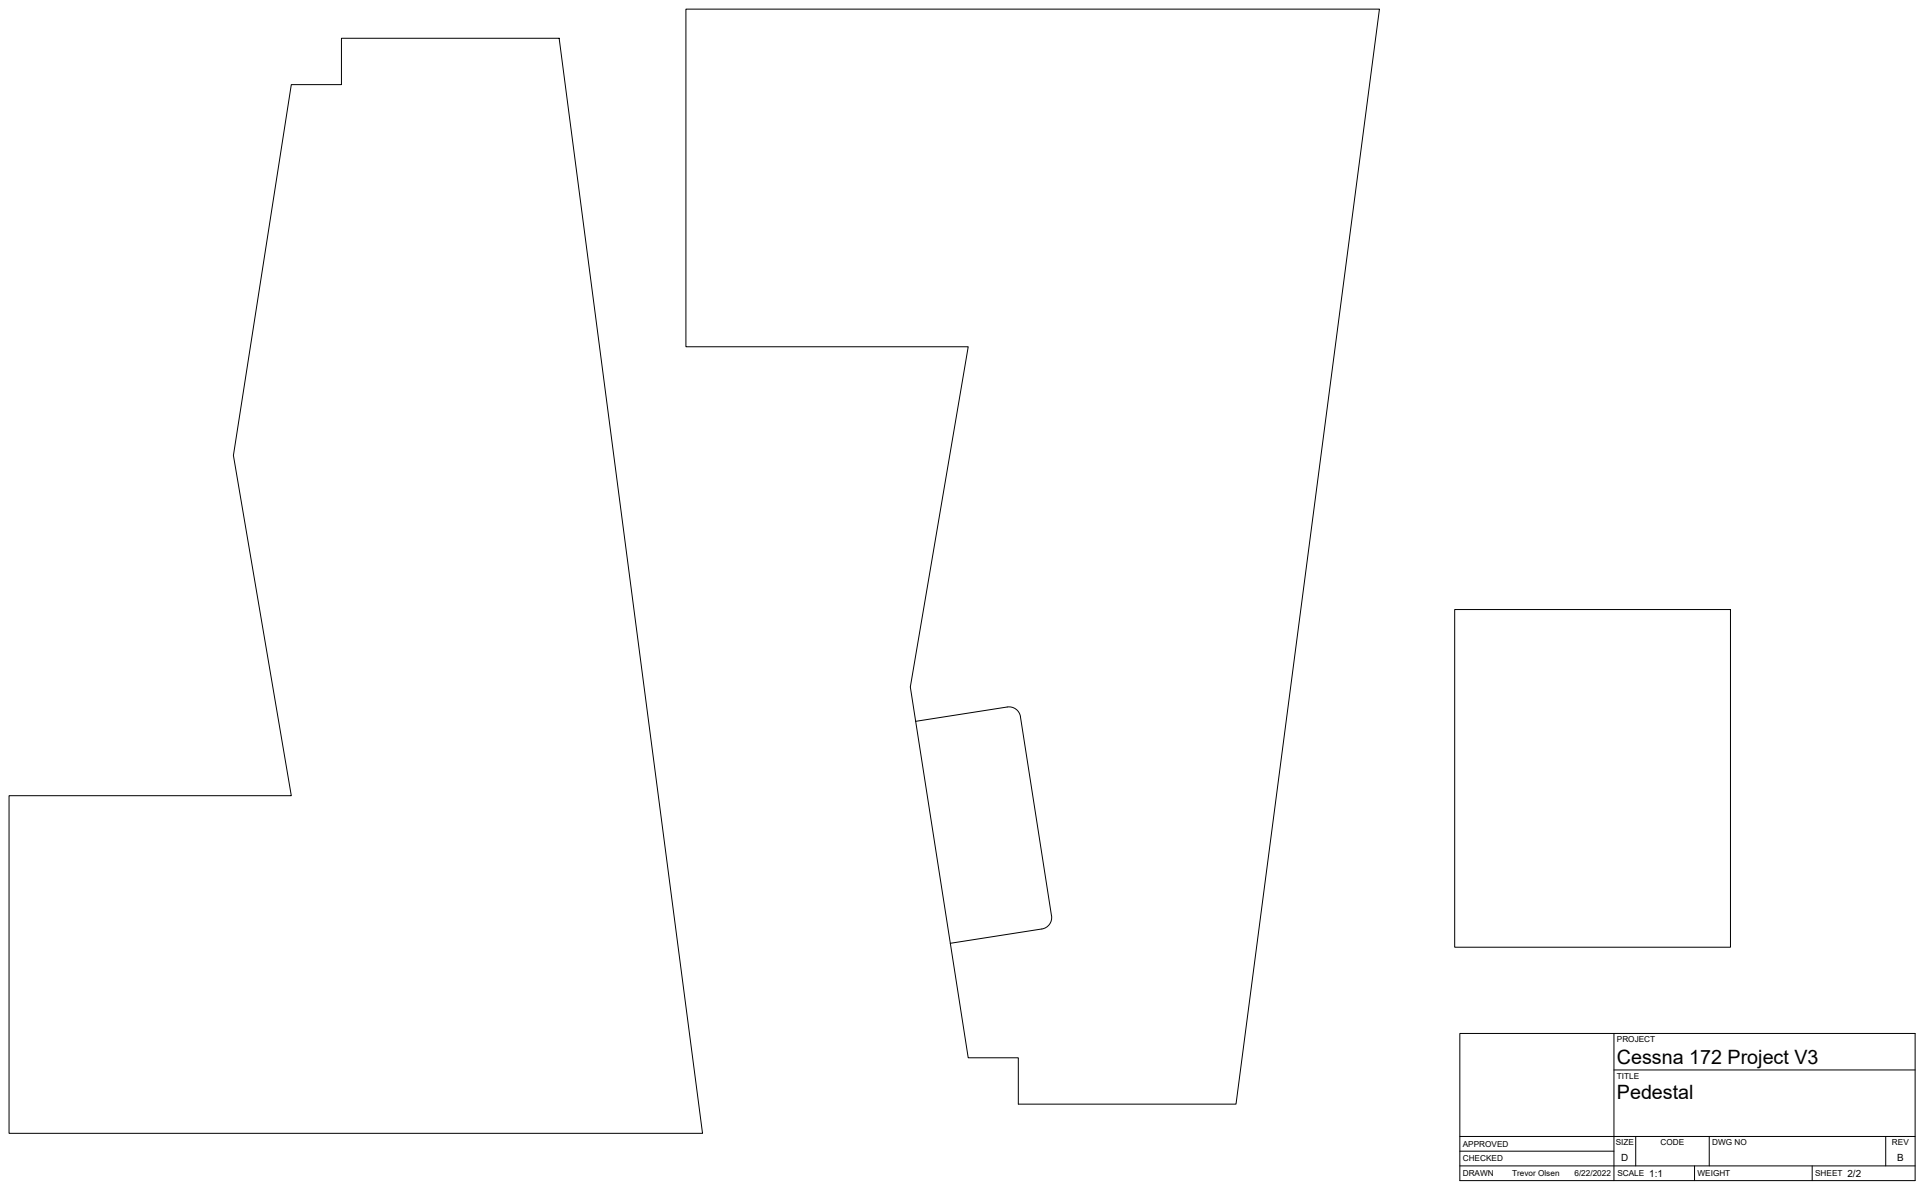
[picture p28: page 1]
SIZE; CODE; DWG NO; REV; Trevor Olsen; Cessna 172 Project V3

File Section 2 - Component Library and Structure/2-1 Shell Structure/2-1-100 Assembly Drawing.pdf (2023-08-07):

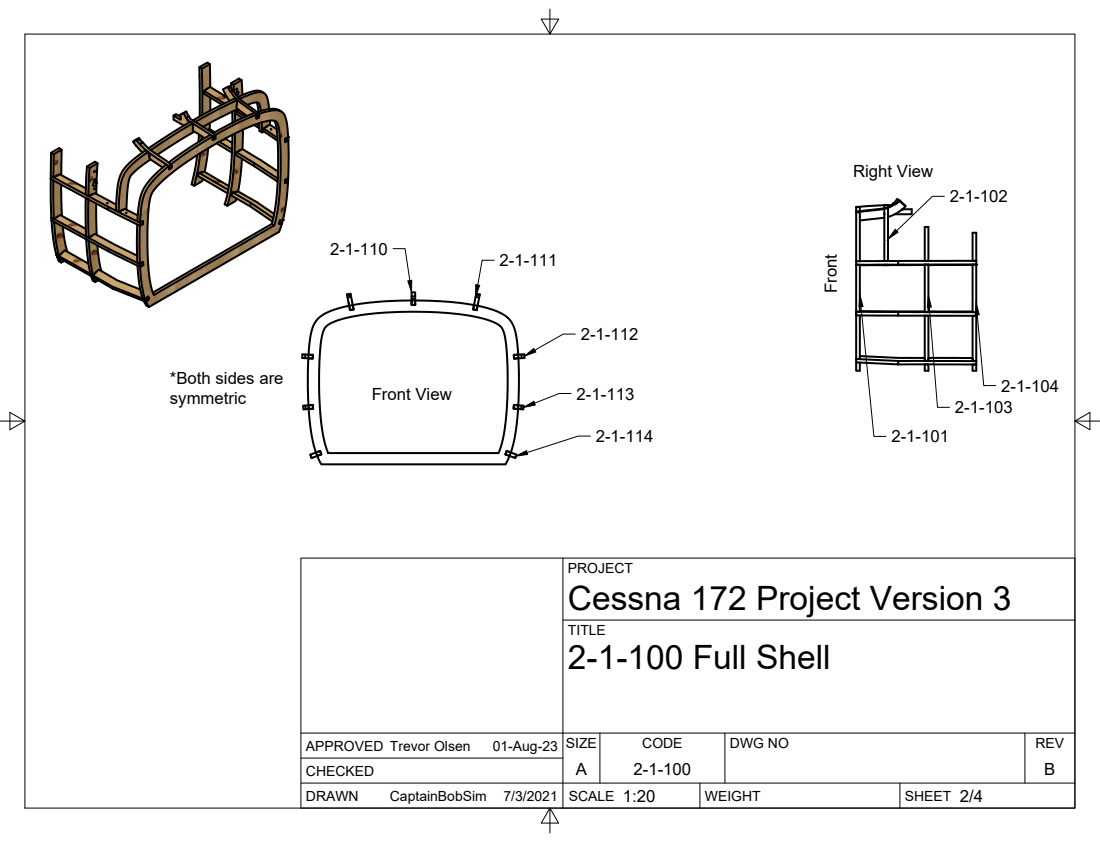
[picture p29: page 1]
SIZE; CODE; DWG NO; REV; Trevor Olsen; 01-Aug-23; symmetric; Front View

Right View Front

*Both sides are

PROJECT
Cessna 172 Project Version 3
2-1-100 Full Shell

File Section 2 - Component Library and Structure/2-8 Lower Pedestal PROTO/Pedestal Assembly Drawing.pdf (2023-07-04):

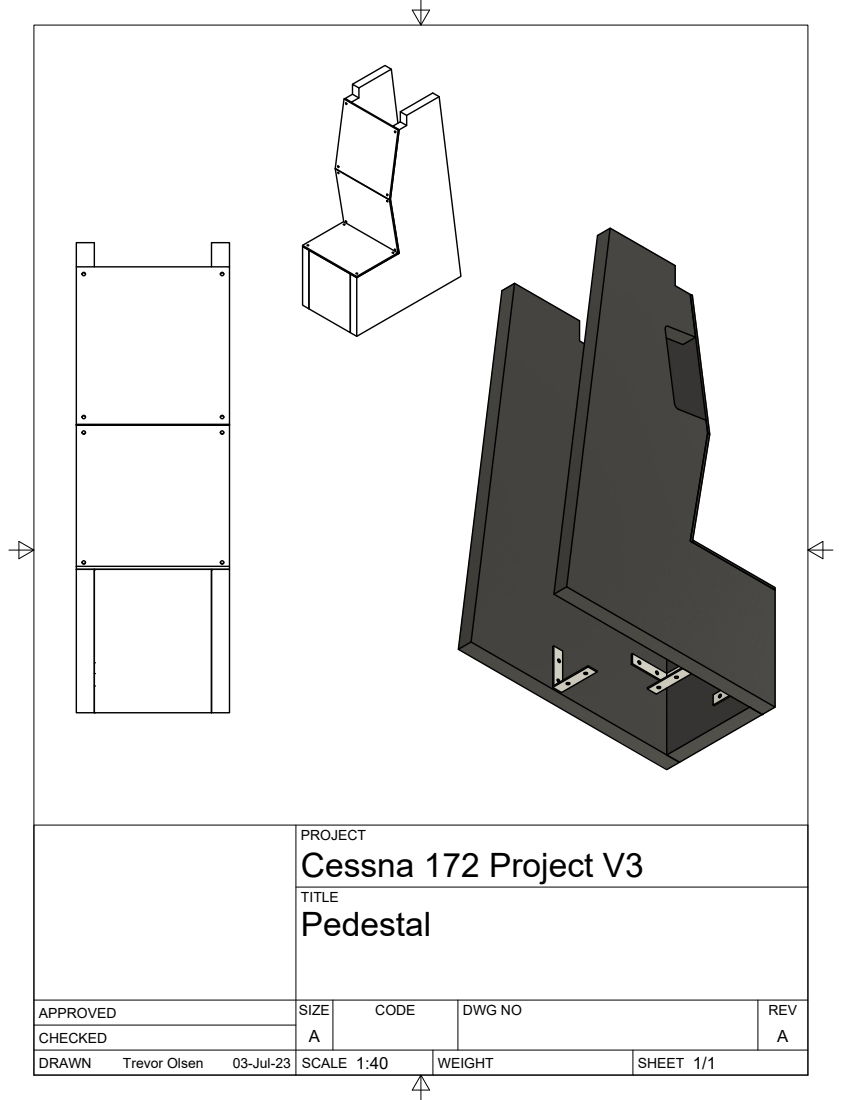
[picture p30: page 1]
SIZE; CODE; DWG NO; REV; Trevor Olsen; 03-Jul-23; Cessna 172 Project V3

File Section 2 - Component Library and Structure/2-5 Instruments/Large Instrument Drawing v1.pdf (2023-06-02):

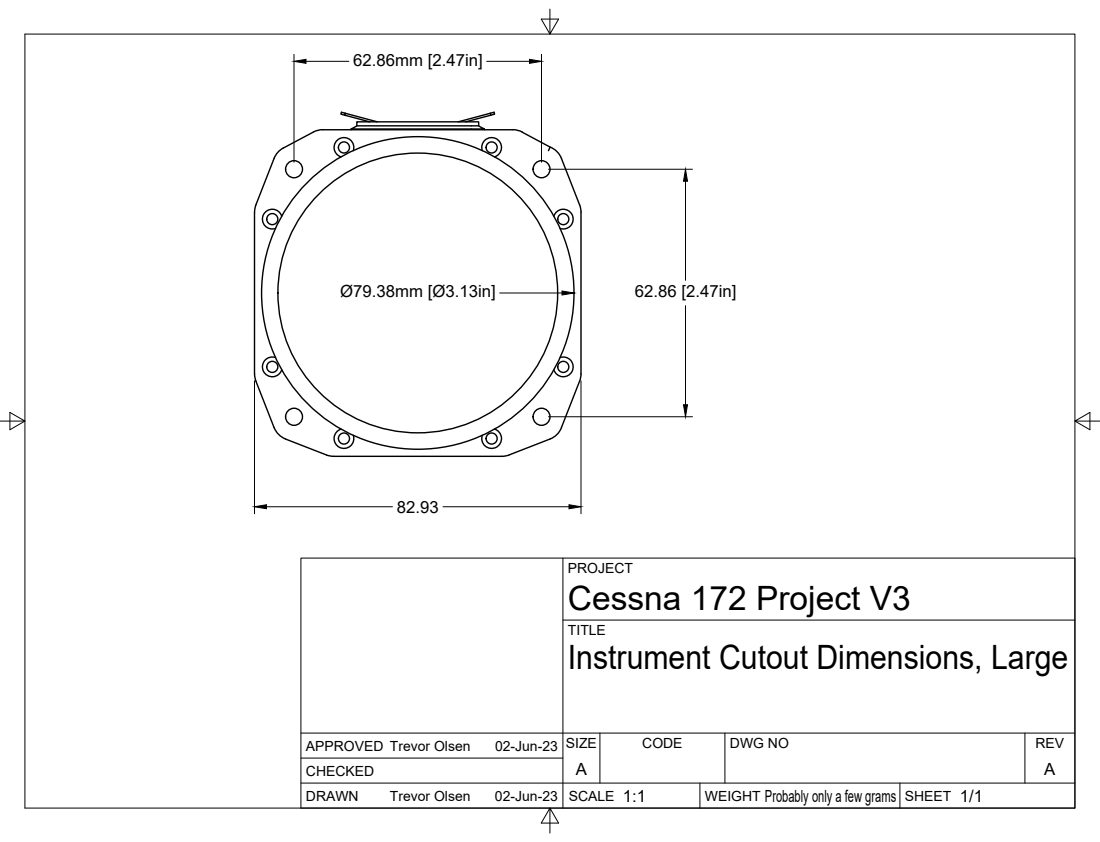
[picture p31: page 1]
SIZE; CODE; DWG NO; REV; Trevor Olsen; 02-Jun-23; Probably only a few grams

PROJECT
Cessna 172 Project V3
Instrument Cutout Dimensions, Large

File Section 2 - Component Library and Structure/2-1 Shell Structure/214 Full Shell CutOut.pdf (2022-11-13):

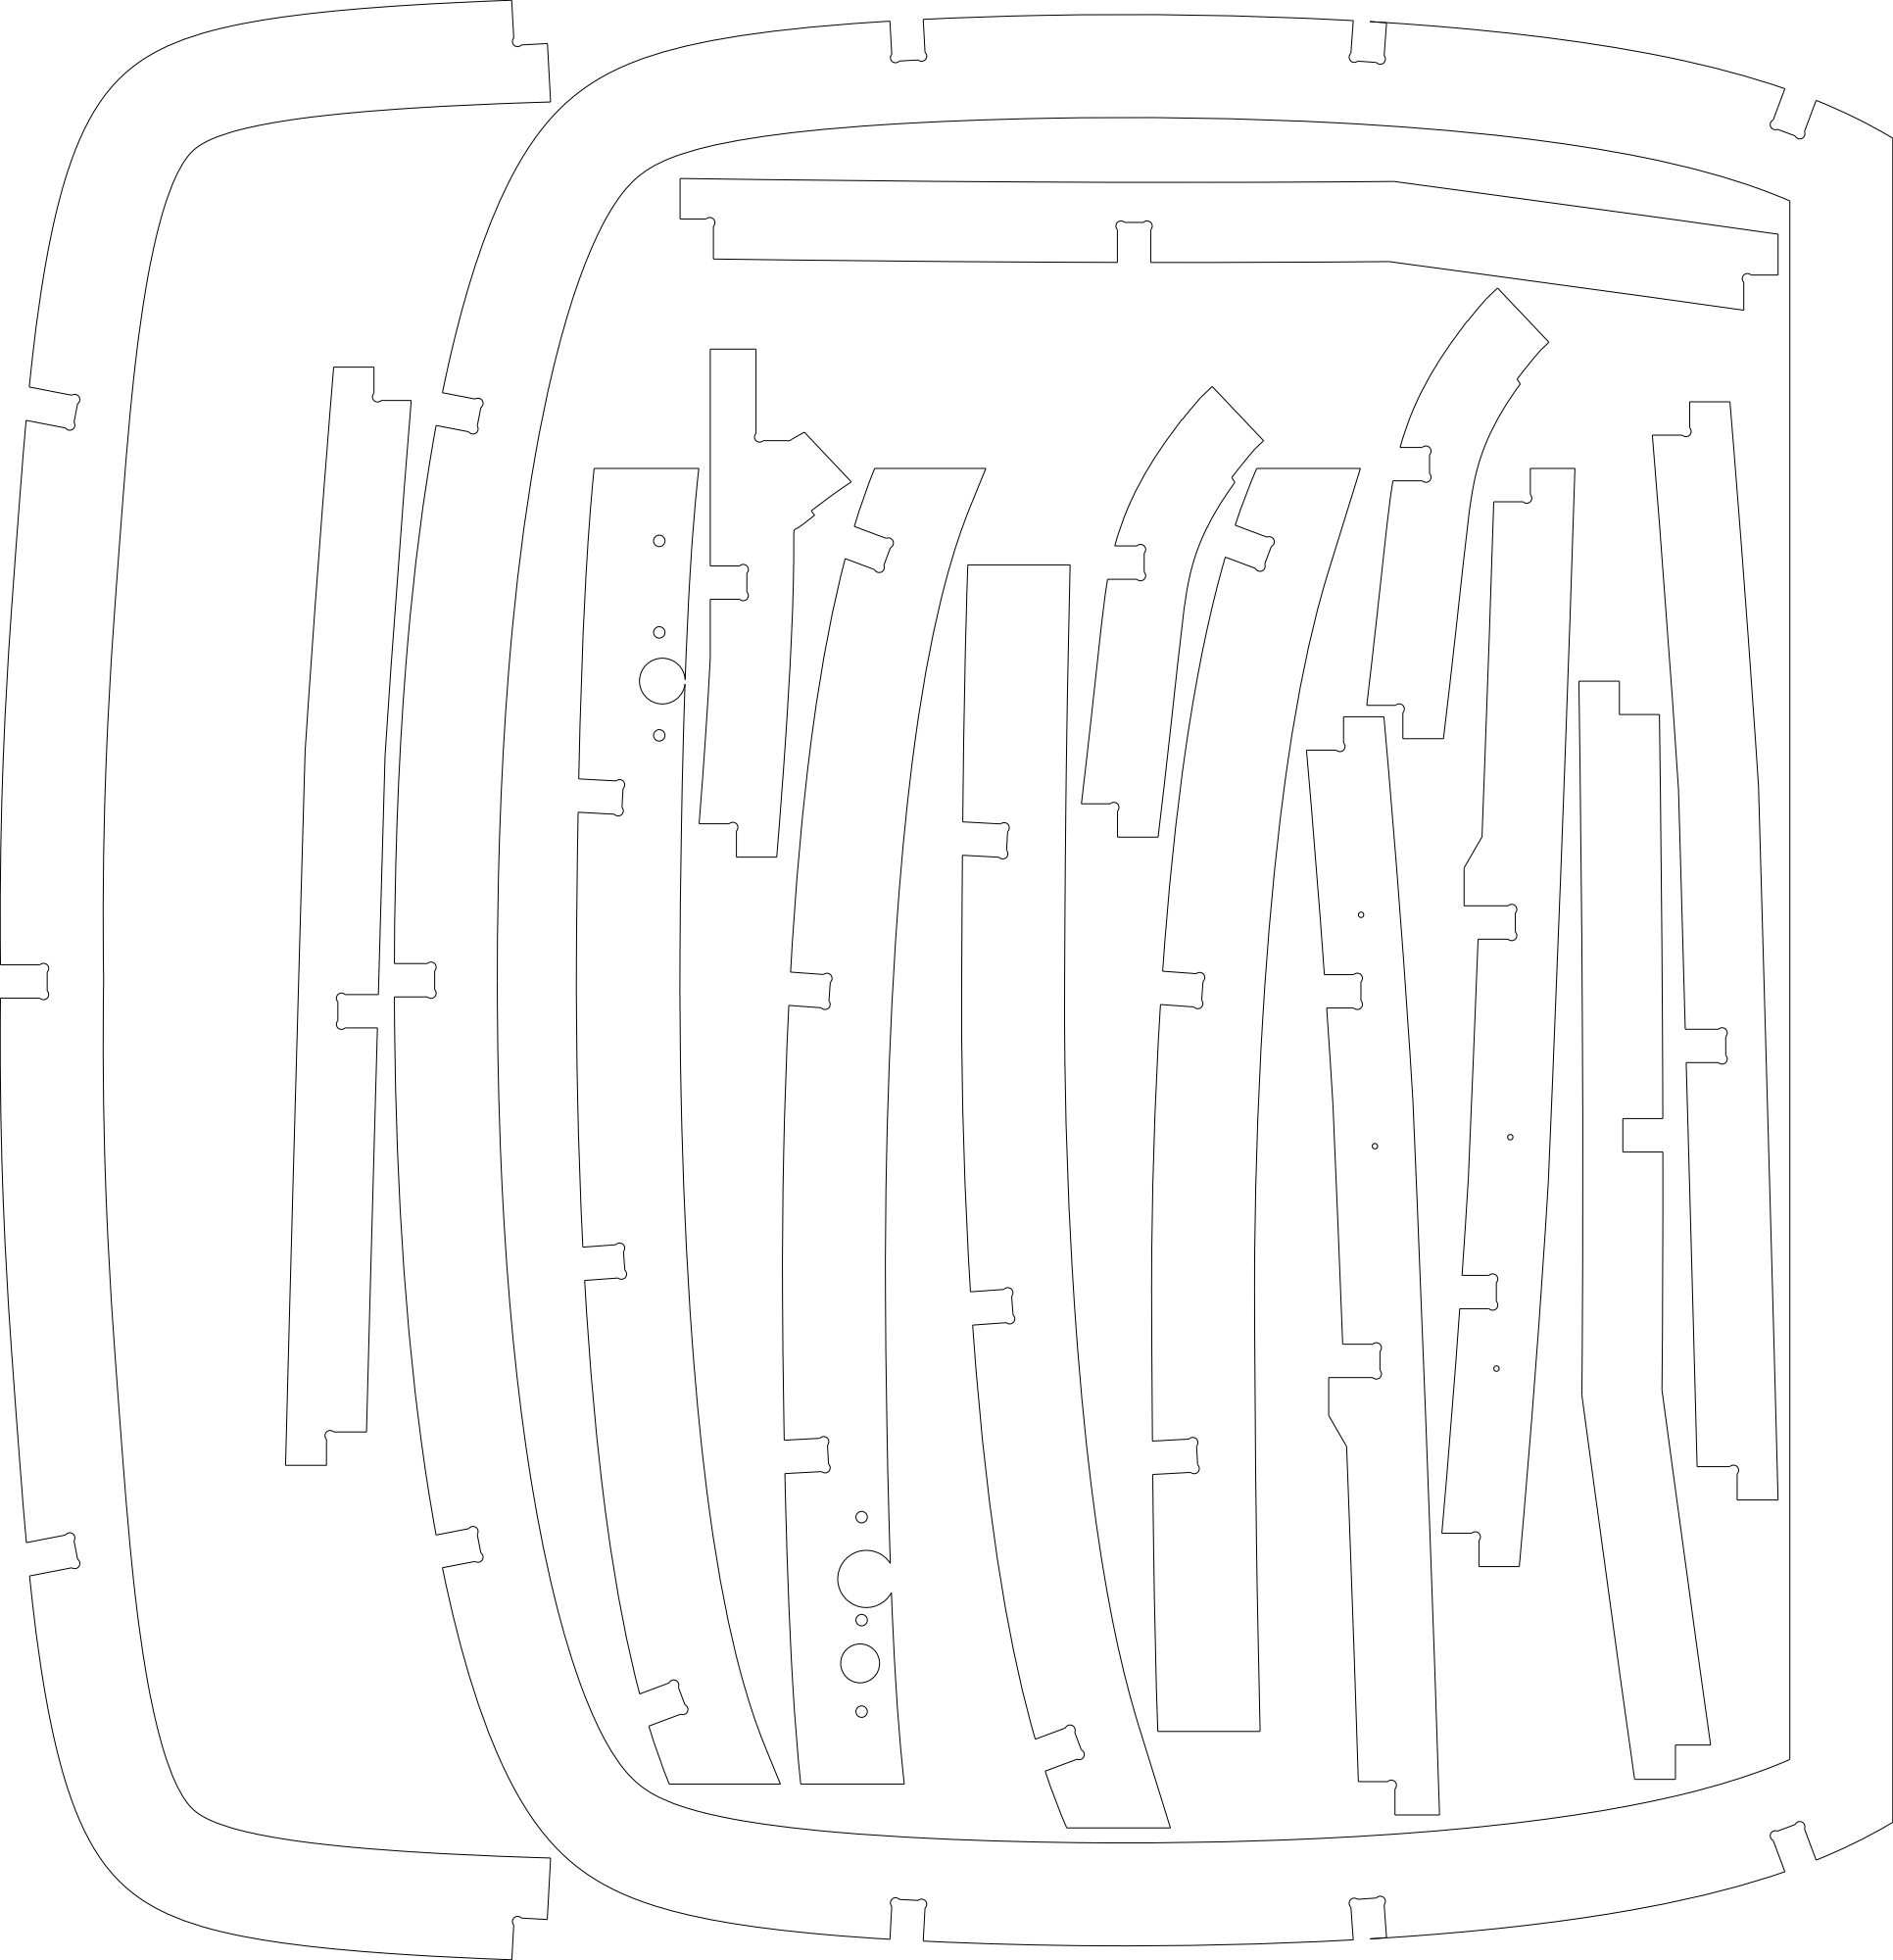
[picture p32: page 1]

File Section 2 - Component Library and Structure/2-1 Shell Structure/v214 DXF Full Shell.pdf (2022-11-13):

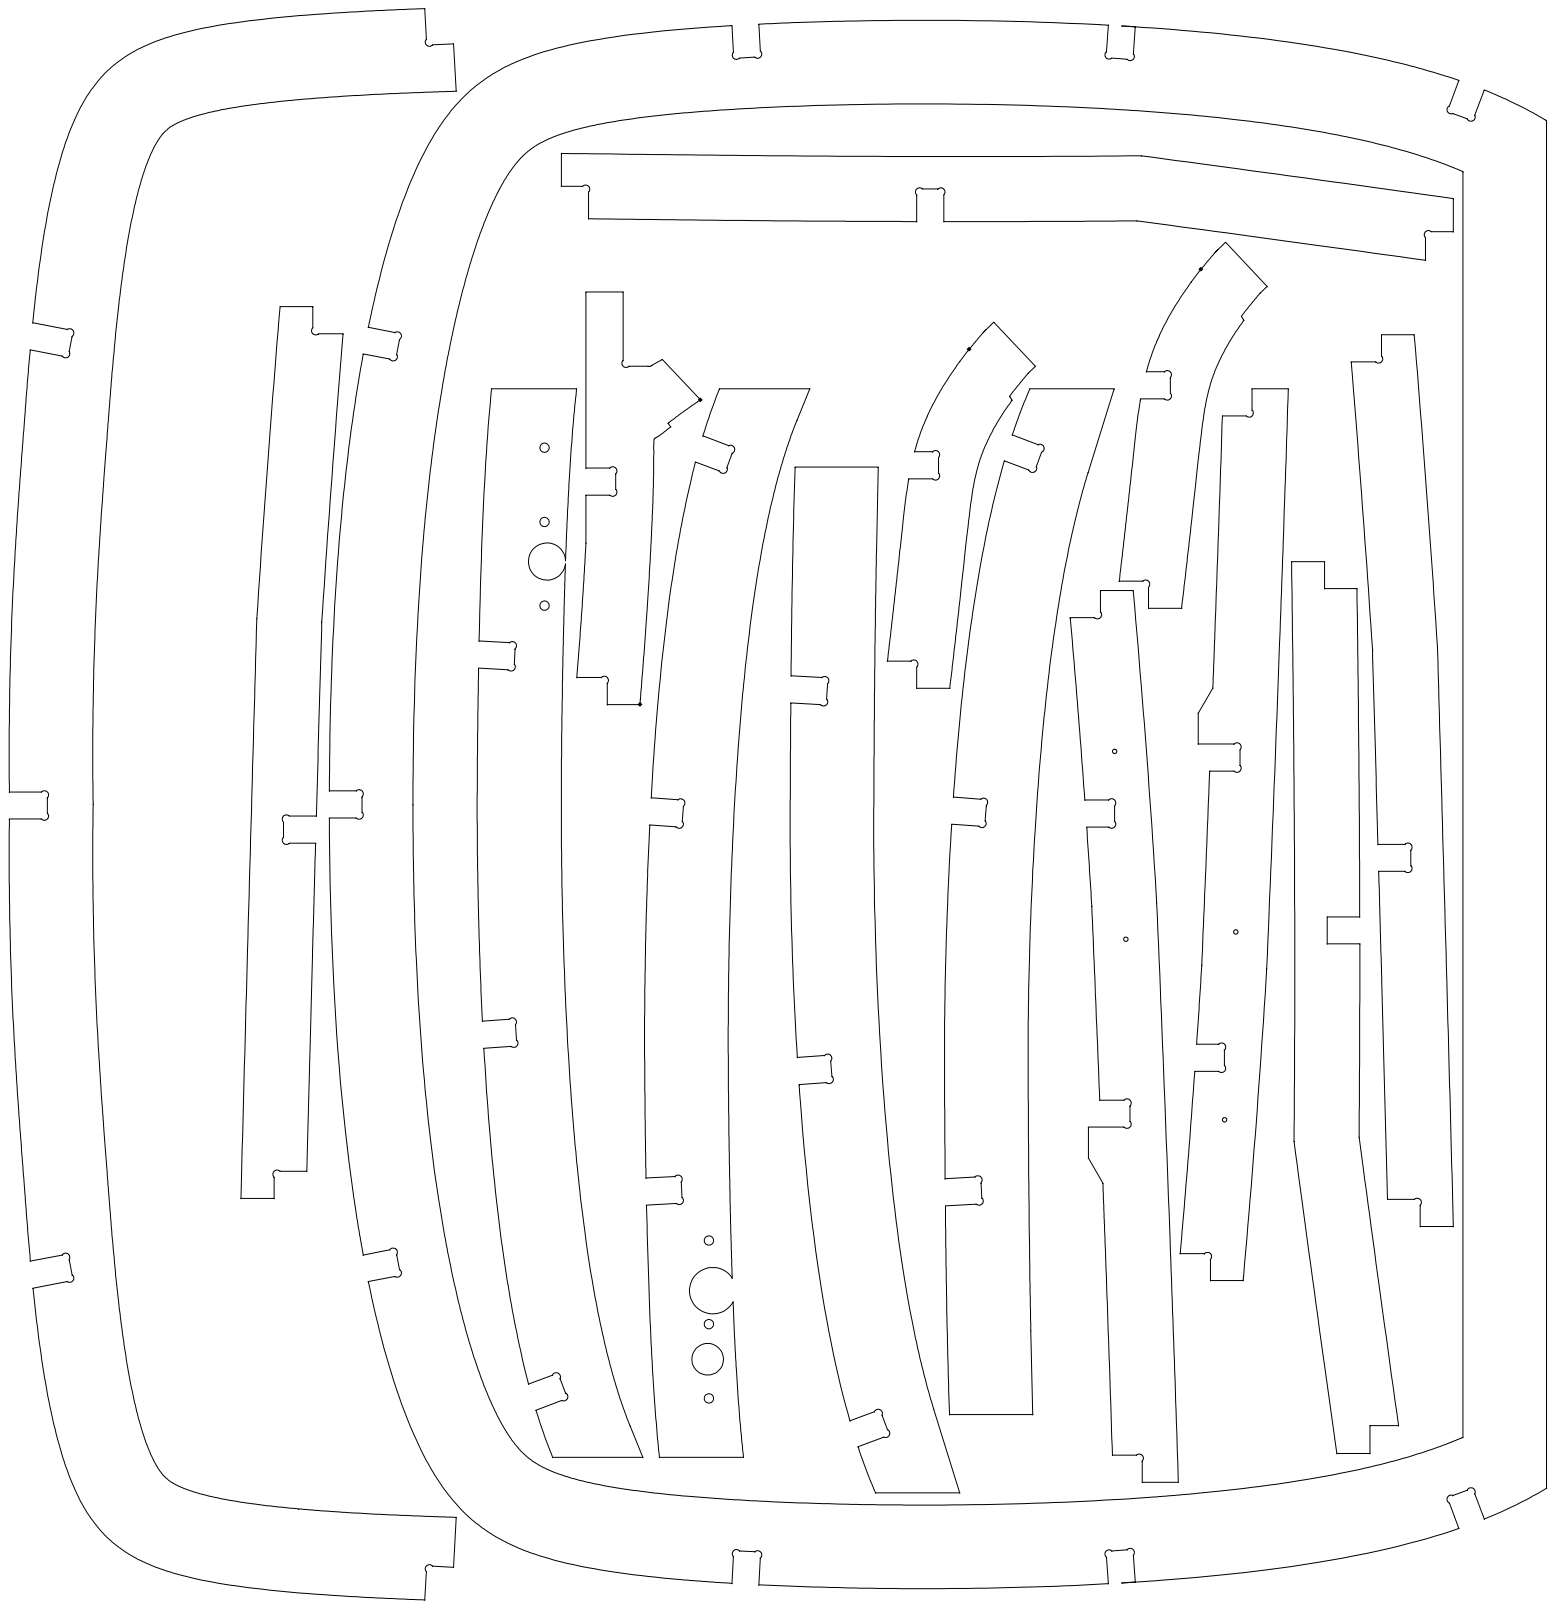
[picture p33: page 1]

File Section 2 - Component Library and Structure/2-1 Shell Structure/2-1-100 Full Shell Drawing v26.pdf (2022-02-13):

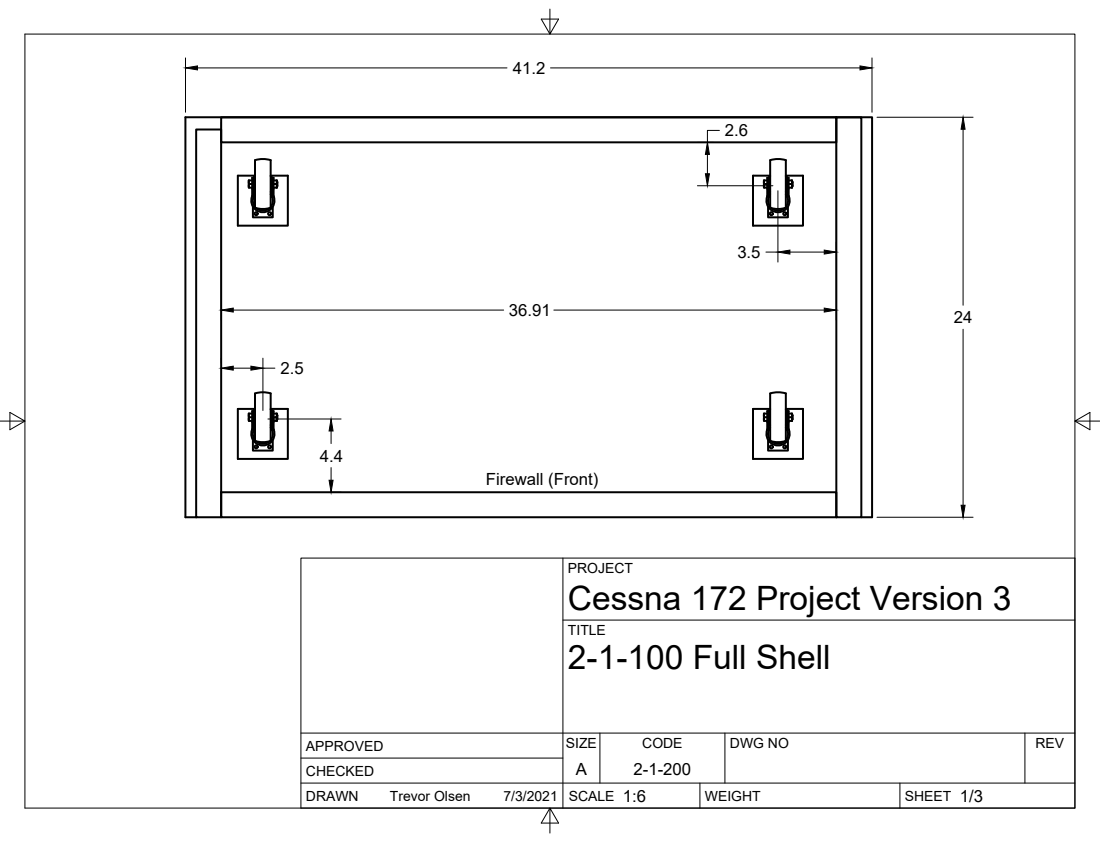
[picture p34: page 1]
SIZE; CODE; DWG NO; REV; Trevor Olsen; Firewall (Front)

PROJECT
Cessna 172 Project Version 3
2-1-100 Full Shell

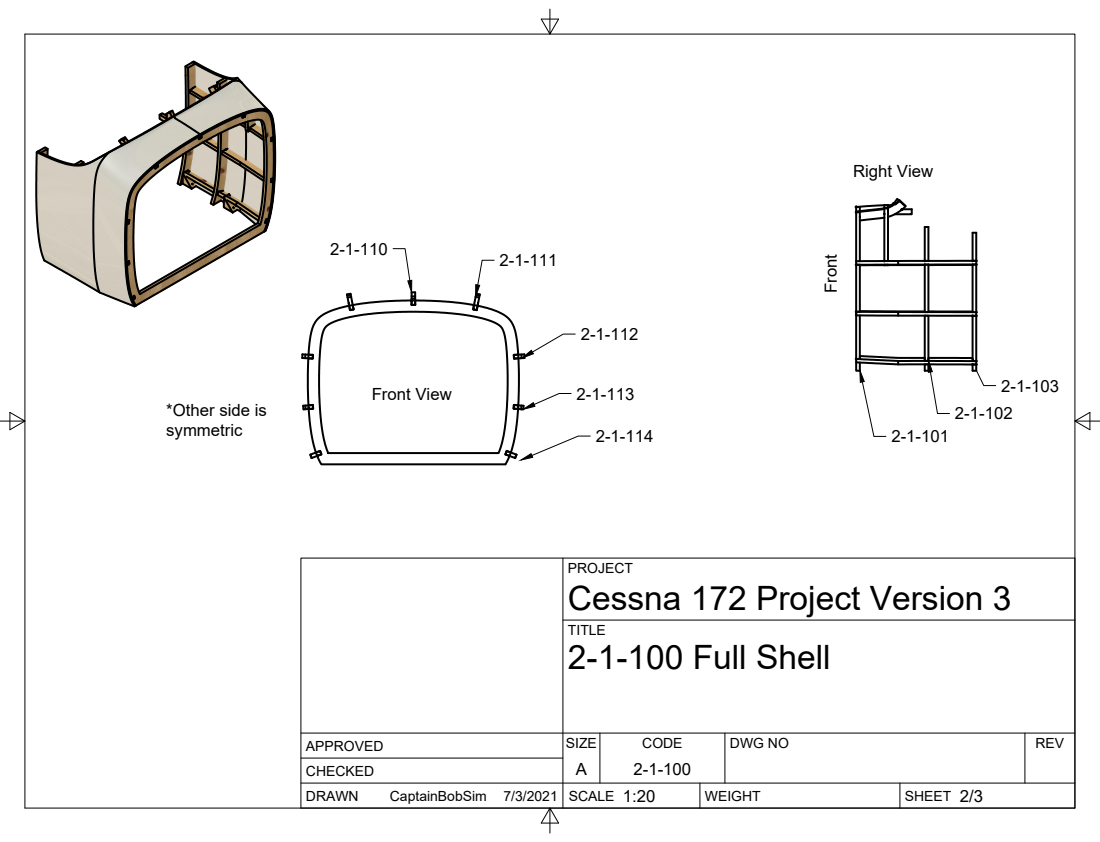
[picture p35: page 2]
SIZE; CODE; DWG NO; REV; Front View

Right View Front

*Other side is
symmetric

PROJECT
Cessna 172 Project Version 3
2-1-100 Full Shell

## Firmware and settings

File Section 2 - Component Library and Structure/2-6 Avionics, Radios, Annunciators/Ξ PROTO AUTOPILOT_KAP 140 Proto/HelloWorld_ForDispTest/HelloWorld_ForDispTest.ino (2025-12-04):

/*

  HelloWorld.ino

  Universal 8bit Graphics Library (https://github.com/olikraus/u8g2/)

  Copyright (c) 2016, olikraus@gmail.com
  All rights reserved.

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
  THIS SOFTWARE IS PROVIDED BY THE COPYRIGHT HOLDERS AND 
  CONTRIBUTORS "AS IS" AND ANY EXPRESS OR IMPLIED WARRANTIES, 
  INCLUDING, BUT NOT LIMITED TO, THE IMPLIED WARRANTIES OF 
  MERCHANTABILITY AND FITNESS FOR A PARTICULAR PURPOSE ARE 
  DISCLAIMED. IN NO EVENT SHALL THE COPYRIGHT HOLDER OR 
  CONTRIBUTORS BE LIABLE FOR ANY DIRECT, INDIRECT, INCIDENTAL, 
  SPECIAL, EXEMPLARY, OR CONSEQUENTIAL DAMAGES (INCLUDING, BUT 
  NOT LIMITED TO, PROCUREMENT OF SUBSTITUTE GOODS OR SERVICES; 
  LOSS OF USE, DATA, OR PROFITS; OR BUSINESS INTERRUPTION) HOWEVER 
  CAUSED AND ON ANY THEORY OF LIABILITY, WHETHER IN CONTRACT, 
  STRICT LIABILITY, OR TORT (INCLUDING NEGLIGENCE OR OTHERWISE) 
  ARISING IN ANY WAY OUT OF THE USE OF THIS SOFTWARE, EVEN IF 
  ADVISED OF THE POSSIBILITY OF SUCH DAMAGE.  
  
  27 Oct 2018:
  
  U8G2_SSD1306_128X64_NONAME_1_4W_HW_SPI u8g2
  make -f Makefile.184.uno
  
   text	   
   8732	    					default, all active
   8500	    -232	    -2.65%		no U8G2_WITH_CLIP_WINDOW_SUPPORT
   8316	    -416	    -4.76%		no U8G2_WITH_FONT_ROTATION
   8606	    -126	    -1.44%	 	no U8G2_WITH_UNICODE
   8692	    -40	    -0.45%		no U8G2_WITH_INTERSECTION
   8328	    -404	    -4.62%	  	no U8G2_WITH_INTERSECTION  no U8G2_WITH_CLIP_WINDOW_SUPPORT
   8718	    -14	    -4.86%		no U8G2_WITH_HVLINE_SPEED_OPTIMIZATION
   8026	    -706	    -8.08%		no U8G2_WITH_FONT_ROTATION   no U8G2_WITH_INTERSECTION  no U8G2_WITH_CLIP_WINDOW_SUPPORT
   
   Some flags depend on each other: `U8G2_WITH_INTERSECTION` is required for `U8G2_WITH_CLIP_WINDOW_SUPPORT`, so `U8G2_WITH_INTERSECTION` is partly active as long
   as `U8G2_WITH_CLIP_WINDOW_SUPPORT` is requested.
   
*/

#include <Arduino.h>
#include <U8g2lib.h>

#ifdef U8X8_HAVE_HW_SPI
#include <SPI.h>
#endif
#ifdef U8X8_HAVE_HW_I2C
#include <Wire.h>
#endif


/*
  U8g2lib Example Overview:
    Frame Buffer Examples: clearBuffer/sendBuffer. Fast, but may not work with all Arduino boards because of RAM consumption
    Page Buffer Examples: firstPage/nextPage. Less RAM usage, should work with all Arduino boards.
    U8x8 Text Only Example: No RAM usage, direct communication with display controller. No graphics, 8x8 Text only.
    
  This is a page buffer example.    
*/

// Please UNCOMMENT one of the contructor lines below
// U8g2 Contructor List (Picture Loop Page Buffer)
// The complete list is available here: https://github.com/olikraus/u8g2/wiki/u8g2setupcpp
// Please update the pin numbers according to your setup. Use U8X8_PIN_NONE if the reset pin is not connected
//U8G2_SSD1322_240X128_1_4W_SW_SPI u8g2(U8G2_R0, /* clock=*/ 13, /* data=*/ 11, /* cs=*/ 10, /* dc=*/ 9, /* reset=*/ 8);
//U8G2_SSD1322_TOPWIN_240X128_1_4W_SW_SPI u8g2(U8G2_R0, /* clock=*/ 13, /* data=*/ 11, /* cs=*/ 10, /* dc=*/ 9, /* reset=*/ 8);
U8G2_SSD1322_NHD_256X64_1_4W_SW_SPI u8g2(U8G2_R2, /* clock=*/ 52, /* data=*/ 51, /* cs=*/ 53, /* dc=14*/ 49, /* reset=15*/ 50);	// Enable U8G2_16BIT in u8g2.h
//U8G2_SSD1322_NHD_256X64_1_4W_HW_SPI u8g2(U8G2_R0, /* cs=*/ 16, /* dc=*/ 14, /* reset=*/ 15);	// Enable U8G2_16BIT in u8g2.h

// End of constructor list

void setup(void) {

  u8g2.begin();  
}

void loop(void) {
  u8g2.firstPage();
  do {
    //u8g2.drawHLine(0,0,10);
    //u8g2.drawHLine(0,31,10);    
    u8g2.setFont(u8g2_font_ncenB10_tr);
    u8g2.drawStr(0,20,"Hello World!");
    u8g2.drawStr(20,40,"Hello World!");
  } while ( u8g2.nextPage() );
  delay(1000);
}

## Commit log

2021-03-01 3.1.2021 Update, Minor bugfixes and skinnyified
    3.1.2021 Update, Minor bugfixes and skinnyified profiles to use less plywood
    Put Stringers and Profile 2 on same sheet to save paper, plywood and glue.
    [0-1 V5 Form Shell Assembly for Splitting v19.step, 1-1 Shell Complete Assy v49.step]
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2021-09-08 UPDATE 9.8.2021
    WARNING Section 1 and 2 have been "Fattened" but not "Healed". DO NOT MAKE THESE ASSYS UNTIL THEY HAVE BEEN HEALED
    [0-0 Complete 172 Assy_v15.f3d, 0-0 Complete 172 Assy_v15.step, 0-1 CANVAS for Reference_v4.step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]
2021-09-08 Spelled "Contribution" correctly :)
    Just that.
    [01_RehostateKnob_6mm_v2.stl, FuelCutoffKnob_STL.stl, FuelTank_Knob.stl]
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2021-10-06 Added Instrument Panel Prototype
    The instrument panel will be rubish until all instruments have been sized. Included because of multiple viewer requests. Knock yourself out!
    [2A Panel v37.step]
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2021-12-11 12.11.2021 Release! Happy Holidays!
    Updated all folders, preserving PDFs. Now completely up to date.
    [0-0 Complete 172 Assy_v15.f3d, 0-0 Complete 172 Assy_v15.step, 0-0 Complete 172 Assy_v28.f3d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]
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2022-01-10 Update a metric hecking ton of files
    Updated outdated files.
    [1-0 Full Section 1 Assy_v24.f3d, 1-0 Full Section 1 Assy_v24.step, 1-5-000 PC_v2.f3d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]
2022-01-10 Update More Files
    Files need to be updated, okay?!
    [(Tall) Panel JAY VR.stl, 2A-1-000 Panel v82.step, 2A-1-000 Panel_v46.f3d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]
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2022-03-26 Rename folders for user friendliness
    Rename section folders to appear less arbitrary, and more informative.
    [(Tall) Panel JAY VR.stl, 0-1 V3 Form Shell Assembly for Splitting Copy_v1.step, 0-1-000 V5 Form Shell Assembly_v50.step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]
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2022-04-09 Glove box Changes - add finger joint generator
    [Glove Box Without Names.dxf, Glove box.dxf]
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2022-06-05 LED and Stepper 28BYJ Support Added to Airspeed / Generic
    [Airspeed Bezel with LED.stl, Back Plate Stepper 28BYJ-48 Display.stl, Back Plate Stepper 28BYJ-48 Motor Mount.stl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]
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2022-06-22 Add STLs (Yokes and USB Hubs) Move Instruments around
    [Airspeed Bezel.stl, Arduino Mega Holder.stl, Back Plate Stepper Hold.stl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]
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2022-08-22 28BYJ Stepper Version improvements with panel print support
    Made various improvements to the 28BYJ Stepper Design which includes small changes to the front bezel. LED holes moved for better placement and lighting. Screw hole diameters increased to allow for l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
    I moved the Generic Instrument stepper version into the simple instrument folder as they appear to be for the same thing.
    Made new 28BYJ stepper versions for the tachometer and vertical speed indicator. The front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
    [6ix Pack.stl, Airspeed Bezel with LED.stl, Airspeed Bezel.stl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]
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2022-08-23 The Great Rename: Part 2 Revenge of the Tree Structure
    [0-1 V3 Form Shell Assembly for Splitting Copy_v1.step, 0-1-000 V5 Form Shell Assembly_v50.step, 0-1-001 CANVAS for Reference_v5.step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]
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2022-12-19 Create Single Knob Push Loose.stl
    [Single Knob Push Loose.stl]
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2022-12-26 Small Instrument Updates
    Various Updates to small instruments. Added EGT. Ongoing work with sliced panels.
    [2A-1-000 Panel 3D Sliced v31.stl, 6ix Pack.stl, Bezel LED.stl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]
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2023-01-10 1.9.2023 Progress
    Transponder, Reorganize, Update Templates, KAP 140
    [Alternate Static Knob.stl, Backing and Mount.stl, Backing plate.stl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]
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2023-01-10 Shorten names to avoid errors
    [Airspeed Bezel.stl, Airspeed Indicator v102.step, Back Plate DXF for decal design.dxf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]
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2023-02-10 Add arduino mount, Circuit Breaker panel, HDG Files
    [Circuit Breaker Panel - Copy.dxf, Circuit Breaker Panel.dxf, DXF Mount Outline.dxf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]
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2023-03-17 March Madness File Rename! (It's absolutely Mad!) Wow! I'm renaming a few folders look at me! I'm so cool!
    [2-3-001 Cessna Yoke Grommet_v2.f3d, 2-3-001 Cessna Yoke Grommet_v2.step, Back.stl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]
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2023-03-22 this might be overwriting things with outdated information maybe?
    [Back Plate Stepper 28BYJ-48 Motor Backplate.stl, Back Plate Stepper 28BYJ-48 Motor Mount.stl, Back Plate Stepper 28BYJ-48 Pully.stl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]
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2023-03-26 Proto Arduino and Rearrange files
    "My world is changing, it's rearranging. something's not really christmas at aaaaaaaaaaaaaaaaaaaaaaaaaaaaaaaaaaaaaaallllllllllll.. Where are you christmas? Why can't I find you? Why have you gone awa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
    [100ft Needle.stl, 10K Needle Gear.stl, 10K Stepper Gear.stl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]
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2023-04-09 Update Circuit Board Files, Template Files, G1000 Files
    [10A Little Button.stl, 15A Little Button.stl, 5A Little Button.stl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]
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2023-04-16 Fixed Missing Servo Plate and Panel Seal Fix
    [Panel Seal LED.stl, Servo Motor Plate.stl]
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2023-04-30 Prune the hedges before the hedges prune you! Update Section 0, restructure, etc.
    [(Tall) Panel JAY VR.stl, 2A-1-000 Panel v175.step, Connector.stl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]
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2023-05-04 Altimeter Update
    Altimeter MCC update
    Readme Update
    Altimeter Knob add 1mm of slack
    [Altimeter Knob.stl]
2023-05-08 Add .mcc and .mfmc files for instruments
    Add DWG dxf conversion, add 6 pack configs
    [v214 DXF Full Shell.dwg]
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2023-05-25 Attitude Fixes and Renaming
    [Backing plate.stl, Bezel LED.stl, Bezel.stl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]
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2023-05-27 Attitude Files Freshen, Small Tolerance Tweaks and software tweaks
    [Backing plate.stl, Pitch Arm (Doohicky).stl, Roll Cover.stl]
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2023-06-07 Flaps and Altimeter Updates
    Decals work and tolerance changes/restructure for altimeter
    [100ft Needle.stl, 10K Needle 2nd Version.stl, 10K Needle Gear.stl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]
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2023-07-07 Thank you Morgan Feldon for the Airspeed Decals!!!!! Also Glareshield :)
    They look awesome!
    [+1,+2 dowel.stl, +2,+3 dowel.stl, -1,+1 dowel.stl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]
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2023-10-04 Switch Panel XP, Steve Sweeney's Master Switch Add (THANK YOU STEVE!!), Upgrade Decals, Rotate files.
    [Bezel.stl, Lil Attitude Guppy.stl, Master_Switch_Body_Top.stl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]
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2024-01-27 Update Pedestal for Dimming collision, Restructure files (rename)
    [3D Printed Casing V4 Older.stl, 3D Printed Casing V5 Newest.stl, 3D Printed Casing.stl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]
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2024-05-29 Rename Yoke, Update Avionics
    Rename Yoke, Update ADF, Update KN-62A, Update KR-87
    [2-3-001 Cessna Yoke Grommet_v2.f3d, 2-3-001 Cessna Yoke Grommet_v2.step, ADF HDG Knob.stl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]
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2024-06-21 Add files via upload
    Replaces Pully to connect to needle, needle shape can be changed for different instruments.
    [Back Plate Stepper 28BYJ-48 Pully.stl, Needle.stl]
2024-06-21 Rename Back Plate Stepper 28BYJ-48 Pully.stl to Back Plate Stepper 28BYJ-48 Pully.stl
    [Back Plate Stepper 28BYJ-48 Pully.stl]
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

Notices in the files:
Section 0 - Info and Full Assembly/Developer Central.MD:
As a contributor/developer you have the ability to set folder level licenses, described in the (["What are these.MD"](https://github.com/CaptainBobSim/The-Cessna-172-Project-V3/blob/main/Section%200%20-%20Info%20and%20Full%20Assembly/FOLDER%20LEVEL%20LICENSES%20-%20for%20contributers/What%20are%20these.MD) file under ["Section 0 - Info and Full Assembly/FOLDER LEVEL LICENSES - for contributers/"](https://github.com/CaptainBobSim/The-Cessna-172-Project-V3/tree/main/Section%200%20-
